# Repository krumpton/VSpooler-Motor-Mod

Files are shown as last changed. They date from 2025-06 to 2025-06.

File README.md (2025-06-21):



# V-Spooler Motor Mod

An addon for the [V-Spooler](https://www.printables.com/model/684376-v-spooler) project to enable automation via an ESP32 and a stepper motor.

Should be fairly easy to port over to the Arduino framework if anybody is so inclined; I’ve kept dependencies minimal and the project layout clean and easy to follow.

## Features
- Filament detection with automatic motor control to start and stop respooling
- Visual status indication using a WS2812B (NeoPixel) LED

## Getting started
See [BUILD_GUIDE.md](./BUILD_GUIDE.md) for detailed assembly instructions, circuit schematics and setup tips.

## Planned improvements
While the main functionality is done, there are still a couple of things that can be improved;
- **Non-linear motor ramp profiles** — currently the motor ramps up and down linearly. Non-linear acceleration could reduce mechanical stress and help avoid skipped teeth, although I haven’t observed missed steps in my tests.
- **TMC2209 UART control or current monitoring** — some filament ends have a small bend that prevents clearing the PTFE tube and runout sensor, causing the motor to stall. This could be addressed by enabling UART mode for stall detection or by monitoring motor current via a shunt resistor and the ESP32 ADC.

## Required Hardware
- **V-Spooler** - only tested with the base model, not any of the extended versions like V-Spooler X. Untested with the desk mount, but it will almost certainly interfere since it uses the same mounting holes. A modified case might be possible to get around this, but I don't use the desk mount so haven't looked into it.
- **ESP32** - I used an ESP32C3 Super Mini for its small form factor, but any should work. I recommend something with 5V logic though, or you'll need to do some level shifting (see below)
    - **Buck converter (optional)** - depends whether your MCU can handle the same voltage as the motor. Some can handle up to 12V or 15V. Mine can't. RIP.
- **TMC2209** - or any motor driver compatible with your microcontroller.
- **Stepper motor** - any which physically fits the project and can be run by your hardware. I used an LDO Nema 17 Speedy Power (the models are based around this, so it's the largest motor which will physically fit the enclosure).
- **Runout sensor** - any which outputs a signal your MCU can interpret. I used an old one from a dead Ender 3 with a 3D printed case to allow PTFE tubing to be inserted. You may need to alter the code depending on whether your runout sensor is active-high or active-low when filament is loaded.
- **WS2812B LED** - others may work, but will need adjusting in code.
- **Button & switch** - any toggle switch and momentary push button. The switch engages/disengages the motor, the button starts/stops respooling.
- **Pulleys & belt** - I use a 3:1 reduction for better torque, but that's probably not necessary for a 1kg spool. Spacing between the pulleys is ~58mm.
- **PSU** - depends on your motor's specs. A 12V 2.5A supply works well with the motor I used here.
- **Misc hardware:**
  - **Veroboard** - the project is designed to use two 25x64mm strips of veroboard for the electronics, with 2.54mm hole pitch. You could also use a single larger strip (or even have a PCB made), I just designed it around what I had on hand. The holes in opposite corners need to be drilled out for the M2 mounting screws. 
  - **Capacitors** - optional, but useful for decoupling/bulk capacitance. I use a small 0.1μF ceramic cap for the LED and TMC2209, 10μF electrolytic bulk cap for the 5V rail and a 470μF electrolytic cap for the 12V rail.
  - **40mm low-profile fan** - I'm using a Noctua 40mm fan to cool the TMC2209 and motor, but any low-profile 40mm fan should work. Just be sure to connect it to the right voltage rail (5V or 12V)
  - **Screws**:
    - 6x M2*4 for the electronics and LED retainer
    - 4x M3*8 + washers to attach the case to the main assembly
    - 8x M3*6 + washers to attach the lid and motor
    - 2x M3*4 to mount the buck converter
    - 4x fan screws (I didn't have any and ended up using M4 screws + nuts, but fan screws would be ideal)
  - **Power passthrough** - depends how you want to get power into the enclosure. I used a panel-mount barrel jack, but you could just use a grommet and hard-wire the power in - you'll need to add some internal strain relief if you go that route though.
  - **JST Connectors (optional)** - I wanted the project to be easily disassembled if needed, so I opted to use JST connectors to connect everything to the veroboard. This is completely optional, you can just solder everything if you want to save a lot of time crimping connectors.

## Tips & Caveats
- **ESP32 Logic Level**: The ESP32 has a logic level of 3.3V, but the WS2812B is expecting a Vih of `Vdd * 0.7`. For a 5V Vdd, that corresponds to a Vih of 3.5V. To account for this, you can either use a level shifter to raise the output from the ESP32 to 5V, or drop the voltage supplied to the LED. I connected the LED's Vdd through a 1N4007 diode, dropping Vdd to ~4.2V. This in turn lowers the expected Vih to ~3V, allowing the ESP32's 3.3V output to properly drive the LED.

## Acknowledgements

 - [esp_ws28xx](https://github.com/okhsunrog/esp_ws28xx) library by @okhsunrog

## Datasheets
- [TMC2209](https://www.analog.com/media/en/technical-documentation/data-sheets/tmc2209_datasheet_rev1.09.pdf)
- [ESP32-C3 Super Mini](https://dl.artronshop.co.th/ESP32-C3%20SuperMini%20datasheet.pdf)
- [LDO NEMA17 Speedy Power Motor](https://www.onetwo3d.co.uk/wp-content/uploads/2022/04/LDO-42STH48-2504AC_RevA.pdf)

## License

[GPL v3](https://www.gnu.org/licenses/gpl-3.0.html)

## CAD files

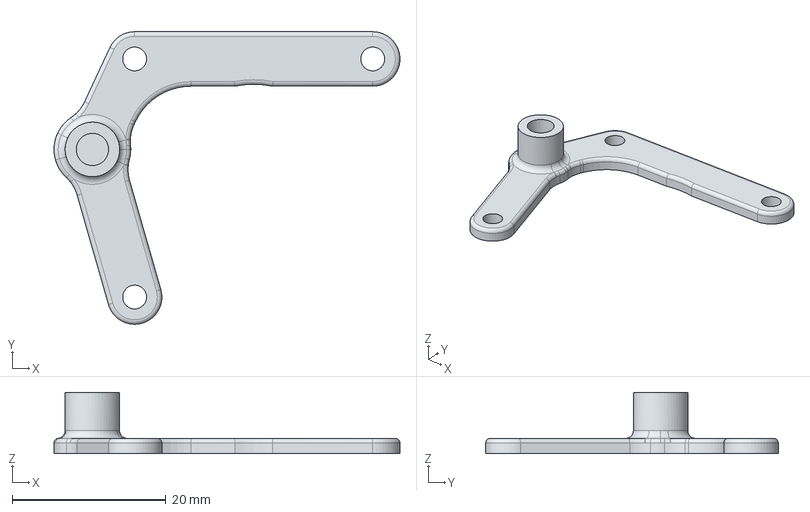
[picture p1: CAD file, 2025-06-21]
models/belt_tensioner/belt_tensioner_body.step
45.0 x 38.1 x 8.00 mm

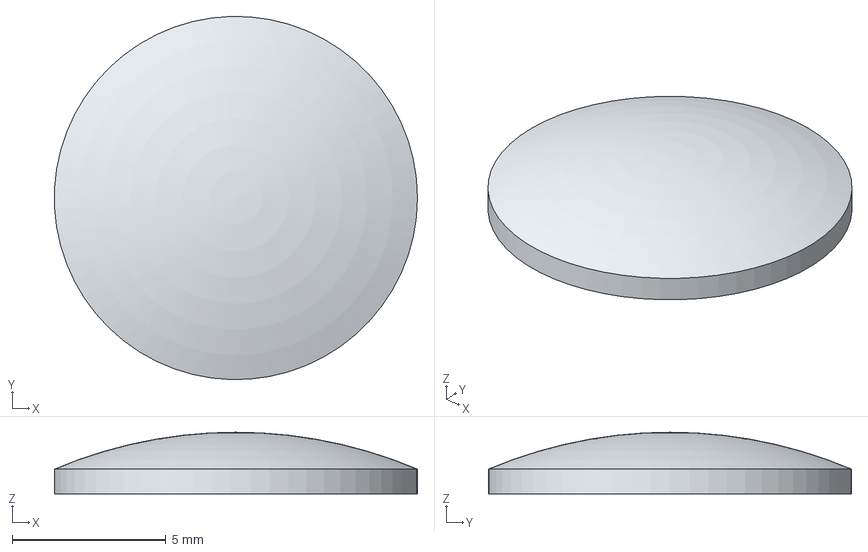
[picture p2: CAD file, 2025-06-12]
models/case/led_diffuser.step
11.8 x 11.8 x 2.00 mm

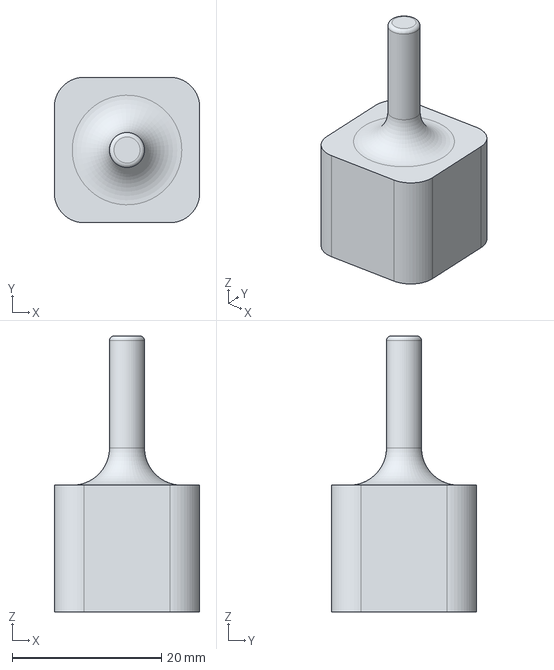
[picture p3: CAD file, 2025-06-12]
models/pulley_adapter/pulley_adapter.step
19.5 x 19.5 x 37.0 mm

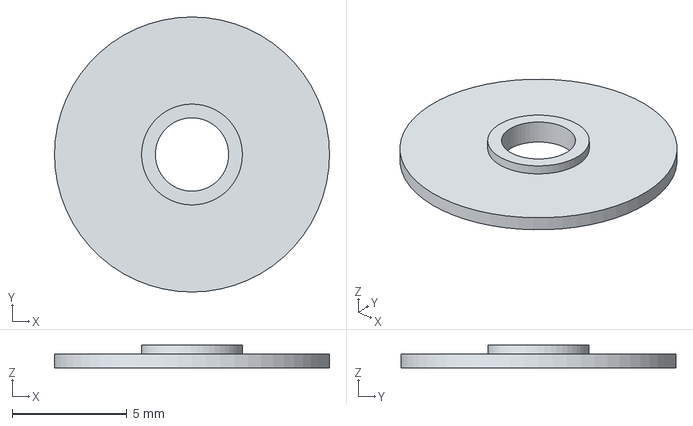
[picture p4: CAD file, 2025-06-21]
models/belt_tensioner/belt_guide.step
12.0 x 12.0 x 1.00 mm

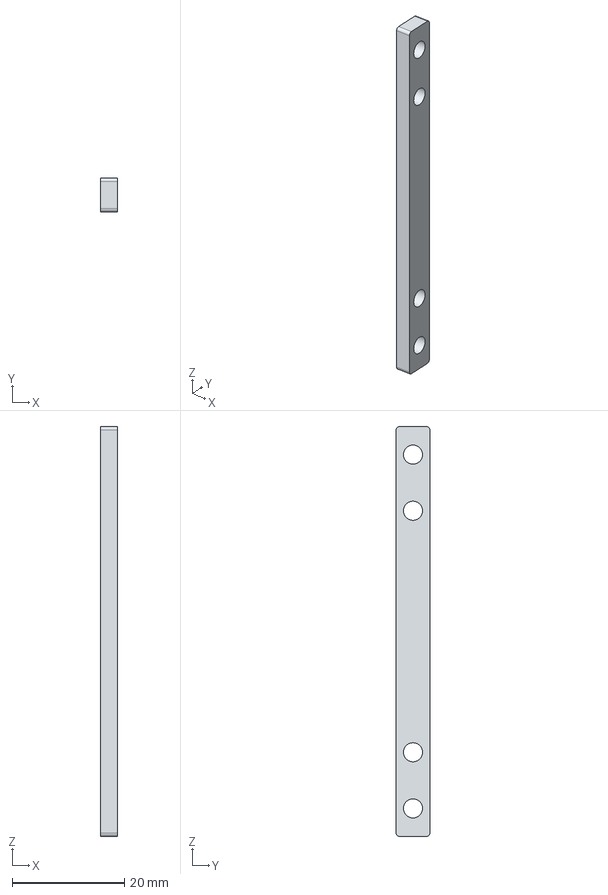
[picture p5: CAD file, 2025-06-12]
models/case/bracket.step
3.00 x 6.00 x 73.0 mm

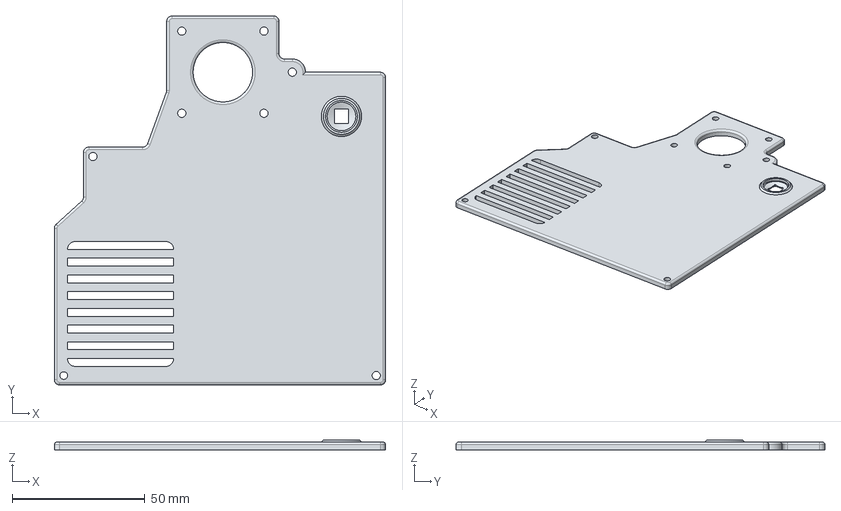
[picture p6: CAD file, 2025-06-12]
models/case/lid.step
125.0 x 139.2 x 3.80 mm

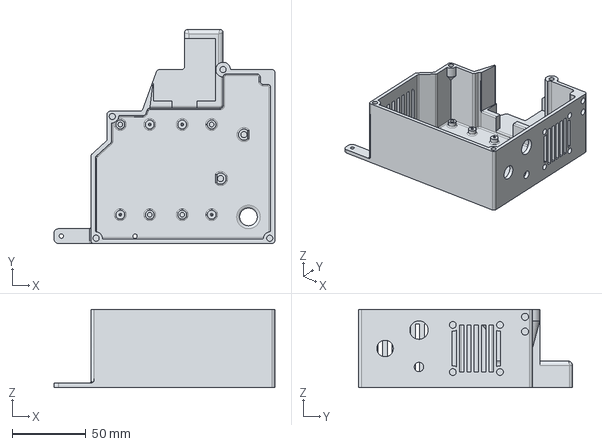
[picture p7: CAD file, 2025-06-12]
models/case/case.step
150.0 x 145.2 x 53.0 mm

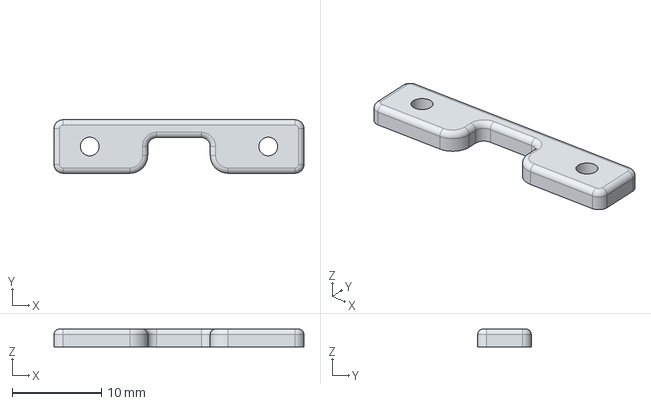
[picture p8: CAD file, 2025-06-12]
models/case/led_retainer.step
28.0 x 6.00 x 2.00 mm

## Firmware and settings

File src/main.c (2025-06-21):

#include "hardware.h"
#include "led.h"

QueueHandle_t hardware_event_queue;

void app_main(void) {
    // create task queue
    hardware_event_queue = xQueueCreate(10, sizeof(hardware_event_t));
    // init LED buffer
    ESP_ERROR_CHECK_WITHOUT_ABORT(led_init(LED_PIN));
    
    // init GPIO & event queue
    hardware_init();

    while (1) {
        hardware_event_t ev;
        hardware_tick();

        // receive messages from hardware.c
        if (xQueueReceive(hardware_event_queue, &ev, 0)) {
            switch (ev) {
                case EVENT_BTN_PRESS_INVALID:
                    led_pulse_single(LED_RED, PULSE_DURATION / 4);
                    break;
                default: break;
            }
        }

        // if the LED is in the middle of doing a single pulse, changing its
        // state will cause it to end early, so check first.
        if (led_state.pulse_mode != PULSE_ONCE) {
            uint32_t colour = LED_WHITE;
            pulse_mode_t pulse_mode = PULSE_NONE;
            int pulse_duration = PULSE_DURATION;

            switch (machine_state & (BITMASK_RUNOUT | BITMASK_RUNNING)) {
                case BITMASK_RUNOUT: // filament unloaded, not running
                    pulse_mode = PULSE_LOOP;
                    pulse_duration = PULSE_DURATION;
                    break;
                case BITMASK_RUNNING: // filament loaded, running
                    pulse_mode = PULSE_LOOP;
                    pulse_duration = PULSE_DURATION * 2;
                    break;
                default: 
                    pulse_mode = PULSE_NONE;
                    break;
            }

            if (!(machine_state & BITMASK_SWITCH)) {
                colour = LED_MAGENTA; // switch = OFF - magenta
            }
            else {
                colour = LED_ORANGE; // switch = ON - orange
            }

            if (machine_state & BITMASK_RUNNING) {
                colour = LED_AZURE; // motor running - blue
            }
            else if (machine_state & BITMASK_PAUSED) {
                colour = LED_INDIGO; // manually paused via button
            }
            else if (machine_state & BITMASK_FINISHED) {
                colour = LED_CHARTREUSE; // stopped due to runout sensor
                pulse_mode = PULSE_NONE;
            }

            led_set_pulse(pulse_mode, pulse_duration);
            led_set_colour(colour);
        }

        led_tick();
    }
}

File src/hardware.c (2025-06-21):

#include "hardware.h"

typedef struct {
    uint32_t debounce_period_us;
    uint64_t last_triggered;
    gpio_num_t pin;
    bool check_level;
} debounce_info_t;

typedef enum {
    CLOCKWISE = 0,
    ANTICLOCKWISE = 1,
} motor_dir_t;

// TMC2209 setup
#define STEP_DELAY_US 100
#define STEP_PULSE_WIDTH_US 20

#define DIR_PIN GPIO_NUM_8
#define STEP_PIN GPIO_NUM_9
#define EN_PIN GPIO_NUM_10

// input pins
#define RUNOUT_PIN GPIO_NUM_1
#define BTN_PIN GPIO_NUM_3
#define SWITCH_PIN GPIO_NUM_4

static QueueHandle_t input_event_queue;
static debounce_info_t button_debounce = {
    .debounce_period_us = 150000,
    .last_triggered = 0,
    .pin = BTN_PIN,
    .check_level = true,
};

// motor speed ramp vars
static int motor_speed_pct = 0;
static int motor_speed_step = 5;
static int motor_speed_max = 1000;
// overall state
uint8_t machine_state;

// - ISR
// just drops events into the task queue to process next tick.
void IRAM_ATTR event_isr_handler(void* arg) {
    hardware_event_t e = EVENT_BTN_PRESS;
    xQueueSendFromISR(input_event_queue, &e, NULL);
}

// - Static functions
// set an individual bit in the bitfield
static void set_bit(uint8_t* input, uint8_t bitmask, uint8_t state) {
    if (state) {
        *input |= bitmask;
    } else {
        *input &= ~bitmask;
    }
}

// set switch and runout bits based on pin state
static void update_machine_state(uint8_t* state) {
    set_bit(&machine_state, BITMASK_SWITCH, !gpio_get_level(SWITCH_PIN));
    set_bit(&machine_state, BITMASK_RUNOUT, !gpio_get_level(RUNOUT_PIN));

    // unset pause bit if filament is unloaded or switch toggled off
    if ((machine_state & BITMASK_PAUSED) &&
        (!gpio_get_level(SWITCH_PIN) || !gpio_get_level(RUNOUT_PIN))) {
        set_bit(&machine_state, BITMASK_PAUSED, 0);
    }
}

// step the motor once & adjust speed as needed
static void motor_step() {
    if (machine_state & BITMASK_STOPPING) {
        if (motor_speed_pct > 0) {
            motor_speed_pct -= motor_speed_step;

            // speed percent shouldn't go below 0, but check to be safe
            if (motor_speed_pct <= 0) {
                motor_speed_pct = 0;
                set_bit(&machine_state, BITMASK_RUNNING, 0);
                set_bit(&machine_state, BITMASK_STOPPING, 0);
            }
        }
    } else { // stop bit not set
        if (motor_speed_pct < motor_speed_max) {
            motor_speed_pct += motor_speed_step;
        }
    }

    // clamp motor_speed_pct to 0 <= x <= motor_speed_max
    if (motor_speed_pct > motor_speed_max) {
        motor_speed_pct = motor_speed_max;
    }

    // make sure we don't divide by 0
    int speed_safe = (motor_speed_pct > 0) ? motor_speed_pct : 1;
    int delay = STEP_DELAY_US * (motor_speed_max / speed_safe);

    // only step the motor if running bit is still set
    if (machine_state & BITMASK_RUNNING) {
        gpio_set_level(STEP_PIN, 1);
        ets_delay_us(STEP_PULSE_WIDTH_US);
        gpio_set_level(STEP_PIN, 0);
        ets_delay_us(delay - STEP_PULSE_WIDTH_US);
    }
}

// debounce input events - could be simplified since only the button is
// debounced now, but might as well leave it as is.
static bool debounce(debounce_info_t* db) {
    uint64_t now = esp_timer_get_time();
    // check time since last trigger
    if (now - db->last_triggered < db->debounce_period_us) {
        return false;
    }

    // make sure level is LOW - prevents triggering when button is released
    if (db->check_level) {
        if (gpio_get_level(db->pin) != 0) {
            return false;
        }
    }

    db->last_triggered = now;
    return true;
}
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

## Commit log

2025-05-22 Basic project structure Updated project structure and created utility functions for reading hardware and controlling indicator LED
2025-05-22 Disable watchdog The task watchdog in FreeRTOS causes issues with the motor spinning continuously, so it needs to be disabled.
2025-06-12 Update board definition Switched the Seeed Xiao ESP32C3 board definition to one more accurate to the actual board I'm using.
2025-06-12 Add models
    [bracket.step, case.step, led_diffuser.step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]
2025-06-20 LED refactor Got rid of the old rgb_t struct in favour of storing hex representations of RGB values as uint32_t, and just shifting off the smallest 3 bytes for the individual R, G and B values. Massi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
2025-06-20 Finish motor logic Motor logic is now complete, in theory the project is finished.
2025-06-21 Add belt tensioner model
    [belt_guide.step, belt_tensioner_body.step]

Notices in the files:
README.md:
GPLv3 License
